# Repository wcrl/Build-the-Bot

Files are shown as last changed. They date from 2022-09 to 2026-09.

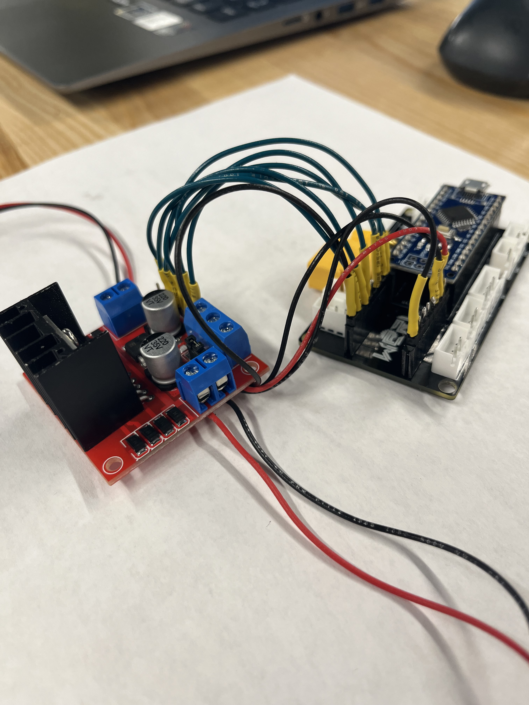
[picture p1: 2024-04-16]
WCRL Parts Library/Motor Drivers/L298N/Arduino Example/L298N_Side.jpg

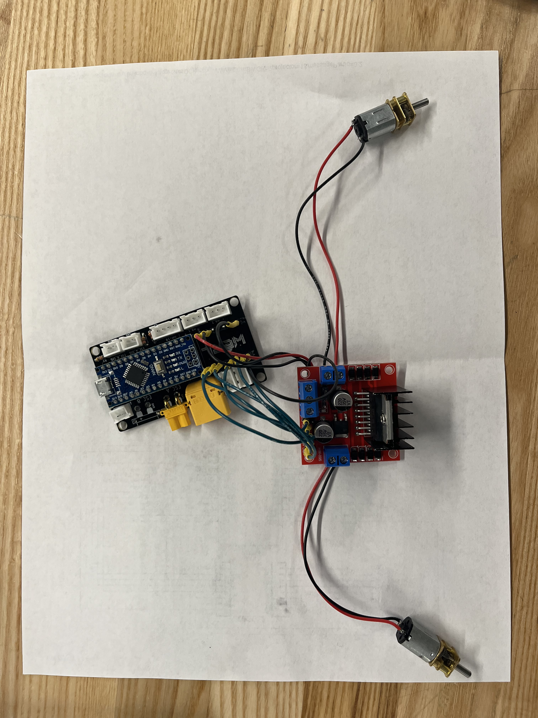
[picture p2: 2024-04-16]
WCRL Parts Library/Motor Drivers/L298N/Arduino Example/L298N_top.jpg

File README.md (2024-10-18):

# About WCRL
Our mission at the Watson Combat Robotics League is to empower collegiate students to develop technical engineering skills through competitive combat robotics. We aim to foster a community of innovation and creativity for students and enthusiasts by providing a platform for designing, building, and testing 3D printed robots in a safe and exciting environment. Our focus is on promoting STEM education by providing an opportunity for practical experience in mechanical design, electrical engineering, and programming as well as peer guidance and resources to make participation increasingly accessible. Through our league, we strive to cultivate the next generation of skilled engineers and innovators who will shape the future of technology and robotics.

# Build-the-Bot
Welcome to the Build-the-Bot platform! Build-the-Bot is an open-source Arduino based robotics platform maintained by the Watson Combat Robotics League at Binghamton University!

To get started, read the [Getting Started Guide](https://github.com/wcrl/Build-the-Bot/blob/453a59d6409c2aacc2f1eb8cd54fe76791a7de1f/Getting%20Started/Getting%20Started.md) and the [3D Printing Guide](https://github.com/wcrl/Build-the-Bot/blob/453a59d6409c2aacc2f1eb8cd54fe76791a7de1f/Getting%20Started/3D%20Printing%20Guide.md). From there, start designing and planning out your bot! 

### Check out our [Website](https://wcrl.github.io/)

### Join our [WCRL Discord](https://discord.gg/YJxM6xMASq)

In order to move to registered status and gain access to more channels make sure you
- Change your discord nickname in this server to your first and last name 
- Fill out our registration form via google forms: https://forms.gle/xkhhvzqmUq5xLZNm7

If you have any questions, please contact us via our discord, or email WCRL@binghamton.edu.

Happy Building!

# Future Development Plans 
- PCB for Battery Cutoff

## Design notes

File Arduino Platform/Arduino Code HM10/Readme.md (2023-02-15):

# ReadME

There are two different sets of code for Bot Control on the Arduino Platform. Due to lack of updates by Dabble, iPhones on iOS 16+ will need to utilize the BitBlue code.

## BitBlue

Note: Pressing and holding does NOT function properly. This is a design conflict in the
BitBlue application. Instead, pressing the button once will trigger an action. Pressing
the button again will end that action.

Controls:

- Forward Arrow: Move Bot Forward
- Back Arrow: Move Bot in Reverse
- Left Arrow: Move Bot to the Left
- Right Arrow: Move Bot to the Right
- A: Competition Attachment at Low Speed
- X: Competition Attachment at High Speed
- B: Not Used
- Y: Not Used
- Start: Not Used
- Select: Not Used

## Dabble

Controls:

- Forward Arrow: Move Bot Forward
- Back Arrow: Move Bot in Reverse
- Left Arrow: Move Bot to the Left
- Right Arrow: Move Bot to the Right
- Triangle: Competition Attachment at Low Speed
- Circle: Competition Attachment at High Speed
- X: Turn off Competition Attachment
- Square: Not Used
- Start: Not Used
- Select: Not Used

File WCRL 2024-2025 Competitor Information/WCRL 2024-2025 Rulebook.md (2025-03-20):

# Watson Combat Robotics League Fall 2024 - Spring 2025 Rulebook

## Version 4.2 | Revised 2025-02-07

## Overview

### Disclaimer

These rules are subject to change with revisions indicated by <u>underlined text</u> and a higher revision number posted above. Competitors will receive notice of changes through the official [WCRL Discord](https://discord.gg/YJxM6xMASq).

Questions answered by an Executive Board Member in the official WCRL discord serve as a revision to the rules and shall be treated as such until the next official revision of the rules is released. The WCRL Executive Board will not answer any rule-pertinent questions in private forms of communication, and if, for whatever reason, these questions are answered privately, they do not serve as official rulings and shall not be treated as such.

The Watson Combat Robotics League Judging Committee and Executive Board reserve the right to remove any team from matches, tournaments, or the league at any time for any reason (including, without limitation, failure to meet safety and/or technical requirements) in its sole and absolute discretion. It is the responsibility of each team to understand and abide by all rules herein.

### Scope

This document outlines the requirements for any team that intends to compete in the 2024-2025 Watson Combat Robotics League (WCRL) (Spring Specific), including the league’s competitions and tournaments.

The Watson Combat Robotics League is an officially recognized Thomas J. Watson College of Engineering and Applied Sciences Student Organization under the oversight of the Electrical and Computer Engineering Department and facilitated by the Watson Combat Robotics League Executive Board.

The following rules have been constructed to be as unrestrictive to the design process as possible while balancing fairness to other competitors, arena damage, scheduling issues, and the safety of any and all competitors, crew, and audience members. **Any discrepancies in the rules will be enforced based on the interpretation of the rules, as written, by the WCRL Executive Board.**

### Definitions

- **Arena:** The arena is approximately 1.83m x 1.83m x 0.91m (6ft x 6ft x 3ft). The arena is outlined in detail in section 6.
- **Bot:** Any movable combat robot that is designed by a WCRL team following the rules as they are outlined herein.
- **Competition:** Any event hosted by the WCRL in which two or more teams compete against each other**
- **Competition Attachment:** A movable, 3D printed component that is attached to a bot that can seriously hinder, halt, or otherwise disrupt the operation of another bot (I.E., a bot's weapon).
- **Control System:** Any device used to send user input to the Bot, i.e. a remote control.
- **Executive Board:** The governing body of the Watson Combat Robotics League, listed in section 4.1.
- **Inspection Checklist:** A document provided to teams prior to the tournament and/or any subsequent tournaments that outlines the most common rule violations to help ensure bots are in compliance with the rules contained herein.
- **Inspection Period:** A portion of the tournament, and/or any subsequent tournaments, in which bots are weighed, measured, and are otherwise verified to abide by these rules. Any bots who do not pass inspection by the end of the inspection period are **not** eligible to demonstrate/compete on that day.  
  - **Note: WCRL Executive Board Officers will be holding open lab hours weekly leading up to the competition and can inspect bots to ensure rule compliance upon team request.**
- **Judging Panel:** The judges of the tournament. These judges will determine the winner of individual matches, and decide two of the three awards, as indicated in section 3.3.
- **League:** The league refers to the entire 2024-2025 competition season
- **Power Switch:** Mechanically and directly shuts off power to the entire bot as explained in section 5.8.
- **Tournament:** A larger competition hosted by the WCRL one weekend per semester.**
- **BOM:** Bill of materials, a complete list of all component parts on the bot including specifications, number of items, and prices.

### Executive Board

- Chairperson: [John Pforte](jpforte1@binghamton.edu)
- League Coordinator: [Ryan Calhoun](rcalhou1@binghamton.edu) 
- Build Technicians: [Sam Abramson](sabrams5@binghamton.edu) | [Ben Sharples](bsharpl1@binghamton.edu) | [Walter Schutz](wschutz1@binghamton.edu) | [Melanie Koren](mkoren1@binghamton.edu) | [Erick Palka](epalka@binghamton.edu) | [Salaj Rijal](srijal@binghamton.edu) | [Mckenzie Viersma](mviersm1@binghamton.edu)
- Competition Coordinator: [Rohan Bajwa](rbajwa1@binghamton.edu)
- Outreach Coordinator: [Haiden Danto-Scanlan](hdantos1@binghamton.edu)
- Social Media Coordinator: [Xinlin Wu](xwu19@binghamton.edu)
- First-Year Ambassadors: [Jay Akasofu](jakasofu@binghamton.edu) | [Alexander Sosa](asosa@binghamton.edu) | [Xinlin Wu](xwu19@binghamton.edu)
- Faculty Advisor: [Professor Wenfeng Zhao](wzhao@binghamton.edu)

### Judging Committee 

- [Professor Douglas Summerville](dsummer@binghamton.edu) (ECE)
- [Professor Scott Craver](Scraver@Binghamton.edu) (ECE)
- [Professor Wenfeng Zhao](wzhao@binghamton.edu) (ECE | Faculty Advisor)
- [Professor Koenraad Gieskes](gieskes@binghamton.edu) (EDD)
- [Professor Melissa Simonik](msimonik@binghamton.edu) (EDD)

_Due to potential scheduling conflicts, the judging committee is subject to change at any time without formal notice in this rulebook. In the event of a tie, a member of the Executive Board will act as the tie-breaking vote._

### Competitors

Teams must register to compete in the WCRL by having each member of their team complete the Google Form Registration and join the Discord. Once all members are registered, the team can reach out to the Eboard with their members and team name, to officially register a team.

Official bot name, team name, and attachment file names must be school-appropriate and cannot contain the word “weapon” or reference to weapons.

- Team and bot names are subject to Executive Board approval.
- Teams may compete with multiple bots if the following criteria are met:
  - Each bot satisfies the requirements.
  - The sum of all robot weights are less than the 1 lb weight limit.

---

## League Overview

The league refers to the entire 2024-2025 competition seasons. During this time teams will brainstorm designs, prototype their design, build bots, compete, and rebuild bots.

### Matches

There will six qualifying competitions per season, held in the Thomas J. Watson College of Engineering and Applied Sciences Fabrication Lab - Engineering Building E1. Two or more teams will compete against each other at each competition, with the competition being live-streamed.

Dates for qualifying competitions and tournaments can be found on our public [WCRL Event Calendar](https://calendar.google.com/calendar/u/0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).

Matches are 2 minutes long, but may be called early for safety concerns or if a winner is decided based on the below criteria.

Pinning:

- For the first 1 minute: A bot can pin another bot for a maximum of 5 seconds before having to release the bot for a minimum of 5 seconds. The 8 second limit will be counted down by the WCRL Executive Board member in charge of the match.
- With less than 60 seconds remaining: If a bot is pinned for more than 5 seconds, the pinned bot will lose. The 5 second limit will be counted down by the WCRL Executive Board member in charge of the match.
  - For teams competing with multiple bots, the rules on pinning are as follows:
    - If bots are equal weights: All bots must be pinned. If a bot is pinned during the eligible time, it may no longer be used.
    - If bots are unequal weights: A majority of the weight must be pinned in order to win. 

Bot Control:

- Bots who lose mobility will lose the match following the same 5 second countdown (i.e., you are not pinned, but your wheels stop being able to move your bot).
- Bots are allowed to lose the ability to control their competition attachment after the initial inspection (outlined below) without forfeiting the match.

### Tournament

There will be one tournament per semester, held in the Binghamton University Innovative Technologies Complex Rotunda. The tournament will run from approximately 9:00 am to 3:00 pm. To be eligible to compete in the tournament, teams must either win one qualifying competition or compete in two qualifying competitions.

More information on the tournament will be released as it becomes available. Any teams not signed in by the end of the inspection period on the day of the tournament will **not** be allowed to compete.

### Awards

There will be three awards presented at the Tournaments, effectively serving as a 1st, 2nd, and 3rd place, respectively:

  1. **Competition Champion:** Presented to the team that wins the double-elimination bracket.
  2. **Competition Runner-Up:** Presented to the team that loses in the finals of the double elimination bracket.
  3. **WCRL Choice:** Presented to the team who excels in bot design, as selected by the judging panel and executive board based on a set of predetermined criteria.

---

## Bot Requirements

### Mobility

- All robots must have easily visible and controlled mobility in order to compete.
Methods of mobility include but are not limited to:
  - Rolling (wheels, tracks or the whole robot)
- No flying, hovering, or otherwise floating bots will be permitted.
  - If a bot is lifted from the floor in the normal course of the match, the bot will not be penalized.
  - Jumping bots are permitted.

### Core Specifications

- The maximum weight for any bot is 453 g (1 lb).
- The maximum height for any bot is determined by the height of the arena.
  - Suggested maximum height is 25 cm.
  - Bots can be weighed on scales made available by the WCRL Executive Board
  - There are no other size restrictions on bots.
    - Note: The arena is 1.83m x 1.83m x 0.91m (6ft x 6ft x 3ft), so keep this in mind for bot design (More on this in section 6.1).
- Each bot shall be entirely 3D printed with an approved 3D Printing material, outlined below:
  - Permissible 3D printing materials include: ABS, PLA (and PLA variants), PETG, Resin, and TPU. Filaments not listed must be approved by the Executive Board.
- The following items are exceptions to the 3D printed requirement: motors, wheels, electronics, axles, bearings, pins, fasteners, rubber bands, belts, adhesives
  - These items must be used in their intended fashion and can not be used to armor the bot
- Flex seal, duct tape, or similar products, are not allowed on the bot.
  - Paint may be allowed on the bot for the purpose of decoration only. Any paint or other coating that adds structural integrity is prohibited.
- Bots cannot intentionally damage the arena

### Competition Attachments (Weapons)

- All bots must have at least one independently powered, 3D printed competition attachment that can seriously affect the operation of another bot. (Note: Bots that have an attachment that cannot cause significant damage to another bot will be seen as _not_ having a competition attachment. This includes flippers that move, but cannot move the weight of the bot with enough power to cause damage).
  - A wedge is permissible, as long as it is accompanied by an additional active competition attachment.
  - Spinning weapons must come to a full stop within 60 seconds of the power
being removed using a self-contained braking system
  - Competition attachments may be swapped between matches, but may require re-inspection.
  - There is no limit on the number of competition attachments on a particular bot.
  - **The following items are not permitted under any circumstances:**
    - Competition attachments that are in any part enhanced with a non-3D printed material
    - Heat and fire are forbidden as weapons. This includes, but is not limited to the
following:
      - Flammable liquids or gases
      - Explosives or flammable solids such as:
        - DOT Class C Devices
        - Gunpowder
        - Cartridge Primers
        - Military explosives, etc.
    - Weapons that require significant cleanup, or in some way damages the arena to
require repair for further matches. This includes but is not limited to:
      - Foams and liquified gases
      - Powders, sand, ball bearings and other dry chaff weapons
    - Projectiles of any type.
    - Entangling Weapons or defenses: these are weapons or defenses that can
reasonably be expected to stop drive train and/or weapon motion by being
wrapped around rotating parts. This includes nets, tapes, strings, and other
entangling materials or devices.
    - Weapons designed to cause invisible damage to the other robot. This includes but is not limited to:
      - Electrical weapons
      - RF jamming equipment
      - RF noise generated by an IC engine
      - EMF fields from permanent/electro-magnets that affect another robot's electronics
    -  Light and smoke based weapons that impair the viewing of robots by an Entrant, Judge, Official or Viewer. This includes, but is not limited to:
       -  Smoke weapons
       -  Lasers
       -  Bright strobe lights
    - Competition attachments that purposefully detach from the bot and are left on the field.
    - Hydraulics or pneumatics.

If a team is concerned about their bot abiding by these rules, WCRL Executive Board members will be holding office hours weekly for the duration of the league. Specific design questions or concerns can also be addressed to any member of the WCRL Executive Board in a private chat.

### Electronics

- [Only LiPo Batteries](https://www.amazon.com/dp/B07Y67CHJT/?coliid=I34AU5484KJY88&colid=1XSIUG9AQPBZB&psc=1&ref_=lv_ov_lig_dp_it) that do not exceed 14 V (4s) nominally are allowed
  - Refer to Appendix 1 for more information on Battery Safety
- The maximum voltage anywhere on the bot is not to exceed 24V.
- Batteries must be sufficiently protected.
  - I.E., If one could jam the blade of a long screwdriver through gaps in the 3D printed shell/frame of the bot and hit the battery, it is not sufficiently protected.
- During the competition, the WCRL executive team will swap drained batteries for fully charged ones to prevent the need for any team to charge their own batteries.
  - If you do not use a WCRL provided battery, they must be charged using a proper battery bag and charger
  - These batteries will be available in designated areas the day of the tournament, and located in EB E1 during the league.
  - Teams must return the provided battery prior to utilizing another one.
- Teams using WCRL provided batteries must have under-voltage protections in place to prevent damaging the batteries. An under-voltage alert buzzer circuit will be available to teams to use in their designs.
- Bots must have a visible LED that is on whenever the bot is on.
- Kill Switches
  - All robots must be able to be FULLY deactivated, which includes power to
drive and weaponry, in under 60 seconds by a manual disconnect.

### Remote Control

- No signal jamming, or deliberate signal interference is permitted.
  - If using Bluetooth controls, renaming the Bluetooth transceiver and adding a password is required to prevent signal interference.
  - Taking control of another team's bot is prohibited
- All control systems must be in compliance with Federal Communications Commission (FCC) regulations, including only accessing and utilizing permitted channels.
- WCRL, WCRL partners, or WCRL sponsors are not liable if teams do not comply with FCC regulations.
- The type and manner of power supply for the controller are left to the team’s discretion as long as the selected design does not aid the performance of the bot beyond allowing driver input to reach the bot.
- There is no restriction on the number of drivers for any one bot as long as all drivers on a team are collectively controlling one single bot.

### Inspection Period

  Each bot will be evaluated for rule compliance by the WCRL Executive Board or other official staff prior to being admitted to any competition or tournament. Failure to comply with the rules or pass inspection may result in disqualification from the match, competition, or tournament.

  **The WCRL Executive Board has the right to refuse any bot deemed particularly dangerous or damaging to people or property.**

  Once a bot passes inspection, the bot will then have a quick inspection prior to each match. This inspection will ensure that the bot is mobile and has a functional competition attachment (as outlined above). _Both_ are required for a bot to be eligible to compete in the match.

### Arena

- The arena is 1.83m x 1.83m x 0.91m (6ft x 6ft x 3ft)
- Note: The floor of the arena is subject to change, and may not be perfectly flat. Testing is recommended prior to the competition to ensure your bot can traverse the arena successfully.
- Once the bot is placed inside the arena, there shall be no further physical interaction with the bot by team members.
- The arena may have additional active and passive field elements to contend with.

---

## 3D Printing

### General Rules

- These parts must not appear to be traditional weapons.
- These competition attachments file names must also not be named in such a way that makes them sound like weapons. (I.e., do not name the item “Blade” or “Knife”).
- Print as soon as possible; there may be delays due to the printing of senior projects which take priority.
- The Watson Combat Robotics League does not print parts for teams nor pay for parts printed by teams.

### Watson Fabrication Lab (Binghamton University Specific)

- Teams can submit models to be printed in the Watson Fabrication Lab by completing the “Request for Fabrication” form posted in the Fabrication lab.
- By printing in the Fabrication Lab, teams agree to any and all Fabrication Lab rules and regulations.

### Emerging Technology Studio (ETS) (Binghamton University Specific)

- [Click here for more information on the ETS.](https://www.binghamton.edu/its/about/organization/technology-support-services/innovation/ets/index.html)
  - Capabilities of printers as well as the print process is outlined on the aforementioned website.
- By printing in the ETS, teams agree to any and all ETS rules and regulations.
- Teams are responsible for the cost of all 3D prints. ETS policy has prints charged to a student’s BUC$ account.
- It is advisable for teams to buy their own filament, and bring it to the ETS, as then there would be no charge to use ETS printers.

---

## Testing

- An arena will be available in the Watson Fabrication Lab (E1)
- A bot's competition attachment can only be tested if the bot is fully within the closed arena.
- This arena is available for use during standard Watson Fabrication Lab hours, or extended hours if a WCRL member is present
- The lid of the arena must be closed during the entirety of the test.
- Teams may use any empty shells in the arena for testing – these shells are in limited supply, and will not be replaced on any set schedule.
  - If your team has any failed bot shells, please consider donating them for other teams to test.
  - Scrimmages are allowed. Please let the WCRL executive team know if you are going to compete against another bot (we’d love to watch!)
  - If your bot starts smoking during one of the tests (not the battery smoking), unplug the battery as quickly and safely as possible.
  - If your battery catches fire, leave the bot where it is inside of the arena, clear the immediate area, and notify one of the shop technicians for assistance.
- If you are concerned about running a test, please run the test during WCRL office hours as we would be happy to assist you.

---

## Use of Workspace

- While using communal spaces such as the Watson Fabrication Lab, ITC, and other spaces, teams must be responsible for:
  - Ensuring all equipment is clean and put away in the proper place.
  - Ensuring that the workspace is properly cleaned.
- Damage to equipment or the arena during bot assembly or testing should be reported to the Executive Board or a shop technician.
- Not adhering to workspace maintenence guidelines will result in action from the Executive Board.  

## Finances

- Each team is limited to a budget cap of $125.
  - 3D printed parts will not be counted towards the budget due to the necessity of spares for multiple matches.
  - The $125 refers to parts on the bot at any given time. Spare parts are not included in the budget cap.
  - This maximum budget for bots includes all control systems, unless you are using a mobile device (cell phone, tablet) for controlling your bot or you have built the controller yourself. In which case, the device itself does not count in the budget.
- Donated or salvaged items must be recorded in the budget as costing an equivalent price to the same part online, sold and shipped by Amazon or Alibaba.
  - If there is any confusion on pricing, the final ruling will be made by the Executive Board.
- WCRL Partners (I.E., Watson student groups) can sponsor their respective teams with any amount of funding. However, each team is still subject to the budget cap.
- Teams must have receipts and a Bill of Materials of all of their parts and pricing available to be reviewed by a judge upon request. Failure to comply with these rules may result in disqualification of a team for award consideration.
  - Teams must use the provided BOM template with accurate pricing to be submitted 24 hours prior to the start of matches and/or tournaments.

---

## Resources

- Check out our [Getting Started Guide](https://github.com/wcrl/Build-the-Bot/blob/main/Getting%20Started/Getting%20Started.md)
- Check out our [Electronics Bill of Materials](https://github.com/wcrl/Build-the-Bot/blob/main/Electronics/Electronics%20BOM.md)

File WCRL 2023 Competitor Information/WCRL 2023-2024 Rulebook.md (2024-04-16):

# Watson Combat Robotics League Fall 2023 - Spring 2024 Rulebook

## Version 4.1 | Revised 2023-04-16

## Overview

### Disclaimer

These rules are subject to change with revisions indicated by <u>underlined text</u> and a higher revision number posted above. Competitors will receive notice of changes through the official [WCRL Discord](https://discord.gg/YJxM6xMASq).

Questions answered by an Executive Board Member in the official WCRL discord serve as a revision to the rules and shall be treated as such until the next official revision of the rules is released. The WCRL Executive Board will not answer any rule-pertinent questions in private forms of communication, and if, for whatever reason, these questions are answered privately, they do not serve as official rulings and shall not be treated as such.

The Watson Combat Robotics League Judging Committee and Executive Board reserve the right to remove any team from matches, tournaments, or the league at any time for any reason (including, without limitation, failure to meet safety and/or technical requirements) in its sole and absolute discretion. It is the responsibility of each team to understand and abide by all rules herein.

### Scope

This document outlines the requirements for any team that intends to compete in the 2023-2024 Watson Combat Robotics League (WCRL) (Spring Specific), including the league’s competitions and tournament.

The Watson Combat Robotics League is an officially recognized Thomas J. Watson College of Engineering and Applied Sciences Student Organization under the oversight of the Electrical and Computer Engineering Department and facilitated by the Watson Combat Robotics League Executive Board.

The following rules have been constructed to be as unrestrictive to the design process as possible while balancing fairness to other competitors, arena damage, scheduling issues, and the safety of any and all competitors, crew, and audience members. **Any discrepancies in the rules will be enforced based on the interpretation of the rules, as written, by the WCRL Executive Board.**

### Definitions

- **Arena:** The arena is approximately 1.83m x 1.83m x 0.91m (6ft x 6ft x 3ft). The arena is outlined in detail in section 6.
- **Bot:** Any movable combat robot that is designed by a WCRL team following the rules as they are outlined herein.
- **Competition:** Any event hosted by the WCRL in which two or more teams compete against each other**
- **Competition Attachment:** A movable, 3D printed component that is attached to a bot that can seriously hinder, halt, or otherwise disrupt the operation of another bot (I.E., a bot's weapon).
- **Control System:** Any device used to send user input to the Bot, i.e. a remote control.
- **Executive Board:** The governing body of the Watson Combat Robotics League, listed in section 4.1.
- **Inspection Checklist:** A document provided to teams prior to the tournament and/or any subsequent tournaments that outlines the most common rule violations to help ensure bots are in compliance with the rules contained herein.
- **Inspection Period:** A portion of the tournament, and/or any subsequent tournaments, in which bots are weighed, measured, and are otherwise verified to abide by these rules. Any bots who do not pass inspection by the end of the inspection period are **not** eligible to demonstrate/compete on that day.  
  - **Note: WCRL Executive Board Officers will be holding open lab hours weekly leading up to the competition and can inspect bots to ensure rule compliance upon team request.**
- **Judging Panel:** The judges of the tournament. These judges will determine the winner of individual matches, and decide two of the three awards, as indicated in section 3.3.
- **League:** The league refers to the entire 2023-2024 competition season
- **Power Switch:** Mechanically and directly shuts off power to the entire bot as explained in section 5.8.
- **Tournament:** A larger competition hosted by the WCRL one weekend per semester.**
- **BOM:** Bill of materials, a complete list of all component parts on the bot including specifications, number of items, and prices.

### Executive Board

- Chairperson: [John Pforte](jpforte1@binghamton.edu)
- Vice-Chairperson: [Luke Riddoch](lriddoc1@binghamton.edu)
- League Coordinator: [Ryan Calhoun](rcalhou1@binghamton.edu) 
- Build Technicians: [Sam Abramson](sabrams5@binghamton.edu) | [Edward Nunez](enunez10@binghamton.edu) | [Ben Sharples](bsharpl1@binghamton.edu) | [Walter Schutz](wschutz1@binghamton.edu) 
- Competition Coordinator: [David Stein](dstein8@binghamton.edu)
- Outreach Coordinator: [Haiden Danto-Scanlan](hdantos1@binghamton.edu)
- Social Media Coordinator: [Mckenzie Viersma](mviersm1@binghamton.edu)
- First-Year Ambassadors: [Melanie Koren](mkoren1@binghamton.edu) | [Erick Palka](epalka@binghamton.edu) | [Salaj Rijal](srijal@binghamton.edu) | [Timothy Tran](ttran14@binghamton.edu)
- Faculty Advisor: [Professor Wenfeng Zhao](wzhao@binghamton.edu)

### Judging Committee 

- [Professor Douglas Summerville](dsummer@binghamton.edu) (ECE)
- [Professor Scott Craver](Scraver@Binghamton.edu) (ECE)
- [Professor Wenfeng Zhao](wzhao@binghamton.edu) (ECE | Faculty Advisor)
- [Professor Koenraad Gieskes](gieskes@binghamton.edu) (EDD)
- [Professor Melissa Simonik](msimonik@binghamton.edu) (EDD)

_Due to potential scheduling conflicts, the judging committee is subject to change at any time without formal notice in this rulebook. In the event of a tie, a member of the Executive Board will act as the tie-breaking vote._

### Competitors

Teams must register to compete in the WCRL by having each member of their team complete the Google Form Registration and join the Discord. Once all members are registered, the team can reach out to the Eboard with their members and team name, to officially register a team.

Official bot name, team name, and attachment file names must be school-appropriate and cannot contain the word “weapon” or reference to weapons.

- Team and bot names are subject to Executive Board approval.
- Teams may compete with multiple bots if the following criteria are met:
  - Each bot satisfies the requirements.
  - The sum of all robot weights are less than the 1kg weight limit.

---

## League Overview

The league refers to the entire 2023-2024 competition seasons. During this time teams will brainstorm designs, prototype their design, build bots, compete, and rebuild bots.

### Matches

There will five matches a month held in the Thomas J. Watson College of Engineering and Applied Sciences Fabrication Lab - Engineering Building E1. Two or more teams will compete against each other at each competition, with the competition being live-streamed.

Dates for matches and tournaments can be found on our public [WCRL Event Calendar](https://calendar.google.com/calendar/u/0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).

Matches are 2 minutes long, but may be called early for safety concerns or if a winner is decided based on the below criteria.

Pinning:

- For the first 1 minute: A bot can pin another bot for a maximum of 5 seconds before having to release the bot for a minimum of 5 seconds. The 8 second limit will be counted down by the WCRL Executive Board member in charge of the match.
- With less than 60 seconds remaining: If a bot is pinned for more than 5 seconds, the pinned bot will lose. The 5 second limit will be counted down by the WCRL Executive Board member in charge of the match.
  - For teams competing with multiple bots, the rules on pinning are as follows:
    - If bots are equal weights: All bots must be pinned. If a bot is pinned during the eligible time, it may no longer be used.
    - If bots are unequal weights: A majority of the weight must be pinned in order to win. 

Bot Control:

- Bots who lose mobility will lose the match following the same 5 second countdown (i.e., you are not pinned, but your wheels stop being able to move your bot).
- Bots are allowed to lose the ability to control their competition attachment after the initial inspection (outlined below) without forfeitting the match.

### Tournament

There will be one tournament per semester, held in the Binghamton University Innovative Technologies Complex Rotunda. The tournament will run from approximately 9:00 am to 3:00 pm. To be eligible to compete in the tournament, teams must either win one qualifying competition or compete in two qualifying competitions.

More information on the tournament will be released as it becomes available. Any teams not signed in by the end of the inspection period on the day of the tournament will **not** be allowed to compete.

### Awards

There will be three awards presented at the Tournaments, effectively serving as a 1st, 2nd, and 3rd place, respectively:

  1. **Competition Champion:** Presented to the team that wins the double-elimination bracket.
  2. **Competition Runner-Up:** Presented to the team that loses in the finals of the double elimination bracket.
  3. **WCRL Choice:** Presented to the team who excels in bot design, as selected by the judging panel and executive board based on a set of predetermined criteria.

---

## Bot Requirements

### Mobility

- The bot must move around in a controlled manner without causing intentional damage to the arena.
- No flying, hovering, or otherwise floating bots will be permitted.
  - If a bot is lifted from the floor in the normal course of the match, the bot will not be penalized.
  - Jumping bots are permitted.

### Bot Control

- The driver(s) must maintain control over all of the bot’s functions at any given time.
- There is **not** an autonomous portion of this competition. This is subject to change in future competitions.

### Core Specifications

- The maximum weight for any bot is 1,000g (1kg).
- The maximum height for any bot is determined by the height of the arena.
  - Suggested maximum height is 25 cm.
  - Bots can be weighed on scales made available by the WCRL Executive Board
  - There are no other size restrictions on bots.
    - Note: The arena is 1.83m x 1.83m x 0.91m (6ft x 6ft x 3ft), so keep this in mind for bot design (More on this in section 6.1).
- Each bot shall be entirely 3D printed with an approved 3D Printing material, outlined below:
  - Permissible 3D printing materials include: ABS, PLA (and PLA variants), PETG, Resin, and TPU. Filaments not listed must be approved by the Executive Board.
- The following items are exceptions to the 3D printed requirement: motors, wheels, electronics, axles, bearings, pins, fasteners, rubber bands, belts, adhesives
  - These items must be used in their intended fashion and can not be used to armor the bot
- Flex seal, duct tape, or similar products, are not allowed on the bot.
  - Paint may be allowed on the bot for the purpose of decoration only. Any paint or other coating that adds structural integrity is prohibited.
- Bots cannot intentionally damage the arena

### Competition Attachments (Weapons)

- All bots must have at least one independently powered, 3D printed competition attachment that can seriously affect the operation of another bot. (Note: Bots that have an attachment that cannot cause significant damage to another bot will be seen as _not_ having a competition attachment. This includes flippers that move, but cannot move the weight of the bot with enough power to cause damage).
  - A wedge is permissible, as long as it is accompanied by an additional active competition attachment.
  - Competition attachments may be swapped between matches, but may require re-inspection.
  - There is no limit on the number of competition attachments on a particular bot.
  - **The following items are not permitted under any circumstances:**
    - Competition attachments that are in any part enhanced with a non-3D printed material
    - Fire/heat.
    - Liquids.
    - Projectiles of any type.
    - Fouling devices such as, but not limited to, glue, nets, fishing line, ball bearings, particulates, etc.
    - EMP generators or other devices intended to damage or jam the opponent bot’s electronics.
    - Bright lights, lasers, deliberate smoke generators, etc., that are distracting or dangerous to vision.
    - Competition attachments that purposefully detach from the bot and are left on the field.
    - Hydraulics or pneumatics.

If a team is concerned about their bot abiding by these rules, WCRL Executive Board members will be holding office hours weekly for the duration of the league. Specific design questions or concerns can also be addressed to any member of the WCRL Executive Board in a private chat.

### Electronics

- [Only LiPo Batteries](https://www.amazon.com/dp/B07Y67CHJT/?coliid=I34AU5484KJY88&colid=1XSIUG9AQPBZB&psc=1&ref_=lv_ov_lig_dp_it) that do not exceed 14 V (4s) nominally are allowed
  - Refer to Appendix 1 for more information on Battery Safety
- The maximum voltage anywhere on the bot is not to exceed 24V.
- Batteries must be sufficiently protected.
  - I.E., If one could jam the blade of a long screwdriver through gaps in the 3D printed shell/frame of the bot and hit the battery, it is not sufficiently protected.
- During the competition, the WCRL executive team will swap drained batteries for fully charged ones to prevent the need for any team to charge their own batteries.
  - If you do not use a WCRL provided battery, they must be charged using a proper battery bag and charger
  - These batteries will be available in designated areas the day of the tournament, and located in EB E1 during the league.
  - Teams must return the provided battery prior to utilizing another one.
- Teams using WCRL provided batteries must have under-voltage protections in place to prevent damaging the batteries. An under-voltage alert buzzer circuit will be available to teams to use in their designs.
- Bots must have a visible LED that is on whenever the bot is on.
- Power Switches
  - There must be a Power Switch on the bot.
    - The power switch must be located on the exterior of the bot
      - Power Switch operation must be simple enough to allow anyone present to use it.
      - Normal Power switch operation cannot require any lifting or tilting of the bot.
      - Switch operation cannot require that a person get in the path of any competition attachment.
      - No tools must be required to utilize the Power Switch.
      - An insertable/removable jumper plug is an approved (and preferred) alternative to other types of Power Switch.

### Remote Control

- No signal jamming, or deliberate signal interference is permitted.
  - If using Bluetooth controls, renaming the Bluetooth transceiver and adding a password is required to prevent signal interference.
  - Taking control of another team's bot is prohibited
- All control systems must be in compliance with Federal Communications Commission (FCC) regulations, including only accessing and utilizing permitted channels.
- WCRL, WCRL partners, or WCRL sponsors are not liable if teams do not comply with FCC regulations.
- The type and manner of power supply for the controller are left to the team’s discretion as long as the selected design does not aid the performance of the bot beyond allowing driver input to reach the bot.
- There is no restriction on the number of drivers for any one bot as long as all drivers on a team are collectively controlling one single bot.

### Inspection Period

  Each bot will be evaluated for rule compliance by the WCRL Executive Board or other official staff prior to being admitted to any competition or tournament. Failure to comply with the rules or pass inspection may result in disqualification from the match, competition, or tournament.

  **The WCRL Executive Board has the right to refuse any bot deemed particularly dangerous or damaging to people or property.**

  Once a bot passes inspection, the bot will then have a quick inspection prior to each match. This inspection will ensure that the bot is mobile and has a functional competition attachment (as outlined above). _Both_ are required for a bot to be eligible to compete in the match.

### Arena

- The arena is 1.83m x 1.83m x 0.91m (6ft x 6ft x 3ft)
- Note: The floor of the arena is subject to change, and may not be perfectly flat. Testing is recommended prior to the competition to ensure your bot can traverse the arena successfully.
- Once the bot is placed inside the arena, there shall be no further physical interaction with the bot by team members.
- The arena may have additional active and passive field elements to contend with.

---

## 3D Printing

### General Rules

- These parts must not appear to be traditional weapons.
- These competition attachments file names must also not be named in such a way that makes them sound like weapons. (I.e., do not name the item “Blade” or “Knife”).
- Print as soon as possible; there may be delays due to the printing of senior projects which take priority.
- The Watson Combat Robotics League does not print parts for teams nor pay for parts printed by teams.

### Watson Fabrication Lab (Binghamton University Specific)

- Teams can submit models to be printed in the Watson Fabrication Lab by completing the “Request for Fabrication” form posted in the Fabrication lab.
- By printing in the Fabrication Lab, teams agree to any and all Fabrication Lab rules and regulations.

### Emerging Technology Studio (ETS) (Binghamton University Specific)

- [Click here for more information on the ETS.](https://www.binghamton.edu/its/about/organization/technology-support-services/innovation/ets/index.html)
  - Capabilities of printers as well as the print process is outlined on the aforementioned website.
- By printing in the ETS, teams agree to any and all ETS rules and regulations.
- Teams are responsible for the cost of all 3D prints. ETS policy has prints charged to a student’s BUC$ account.
- It is advisable for teams to buy their own filament, and bring it to the ETS, as then there would be no charge to use ETS printers.

---

## Testing

- An arena will be available in the Watson Fabrication Lab (E1)
- A bot's competition attachment can only be tested if the bot is fully within the closed arena.
- This arena is available for use during standard Watson Fabrication Lab hours, or extended hours if a WCRL member is present
- The lid of the arena must be closed during the entirety of the test.
- Teams may use any empty shells in the arena for testing – these shells are in limited supply, and will not be replaced on any set schedule.
  - If your team has any failed bot shells, please consider donating them for other teams to test.
  - Scrimmages are allowed. Please let the WCRL executive team know if you are going to compete against another bot (we’d love to watch!)
  - If your bot starts smoking during one of the tests (not the battery smoking), unplug the battery as quickly and safely as possible.
  - If your battery catches fire, leave the bot where it is inside of the arena, clear the immediate area, and notify one of the shop technicians for assistance.
- If you are concerned about running a test, please run the test during WCRL office hours as we would be happy to assist you.

---

## Use of Workspace

- While using communal spaces such as the Watson Fabrication Lab, ITC, and other spaces, teams must be responsible for:
  - Ensuring all equipment is clean and put away in the proper place.
  - Ensuring that the workspace is properly cleaned.
- Damage to equipment or the arena during bot assembly or testing should be reported to the Executive Board or a shop technician.
- Not adhering to workspace maintenence guidelines will result in action from the Executive Board.  

## Finances

- Each team is limited to a budget cap of $125.
  - 3D printed parts will not be counted towards the budget due to the necessity of spares for multiple matches.
  - The $125 refers to parts on the bot at any given time. Spare parts are not included in the budget cap.
  - This maximum budget for bots includes all control systems, unless you are using a mobile device (cell phone, tablet) for controlling your bot or you have built the controller yourself. In which case, the device itself does not count in the budget.
- Donated or salvaged items must be recorded in the budget as costing an equivalent price to the same part online, sold and shipped by Amazon or Alibaba.
  - If there is any confusion on pricing, the final ruling will be made by the Executive Board.
- WCRL Partners (I.E., Watson student groups) can sponsor their respective teams with any amount of funding. However, each team is still subject to the budget cap.
- Teams must have receipts and a Bill of Materials of all of their parts and pricing available to be reviewed by a judge upon request. Failure to comply with these rules may result in disqualification of a team for award consideration.
  - Teams must use the provided BOM template with accurate pricing to be submitted 24 hours prior to the start of matches and/or tournaments.

---

## Resources

- Check out our [Getting Started Guide](https://github.com/wcrl/Build-the-Bot/blob/main/Getting%20Started/Getting%20Started.md)
- Check out our [Electronics Bill of Materials](https://github.com/wcrl/Build-the-Bot/blob/main/Electronics/Electronics%20BOM.md)

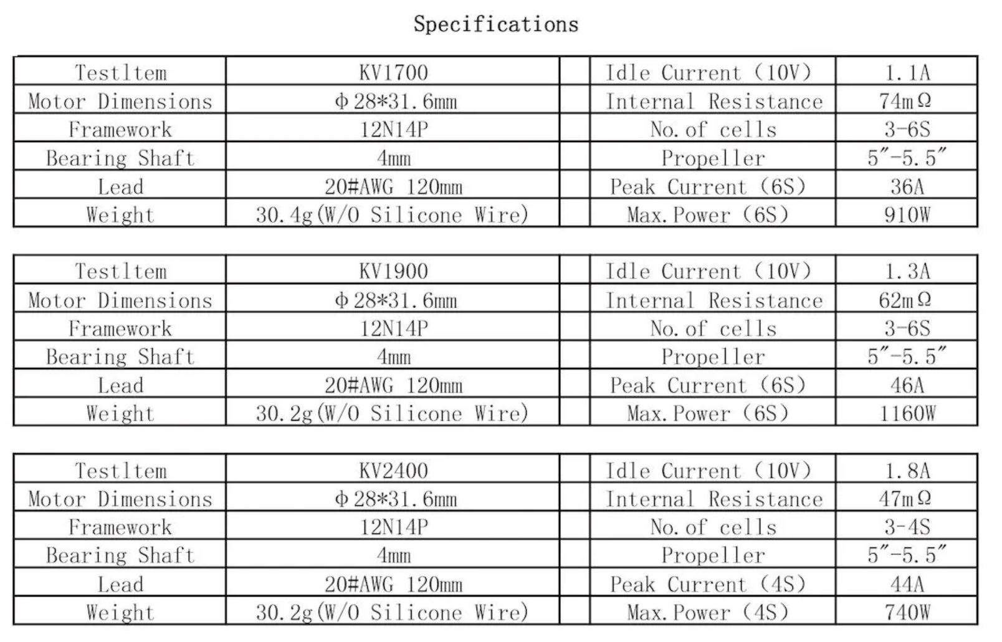
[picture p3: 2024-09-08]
WCRL Parts Library/BLDC Motors/EMAX ECO II Series 2306/EMAX ECO II Series 2306 Specs.png

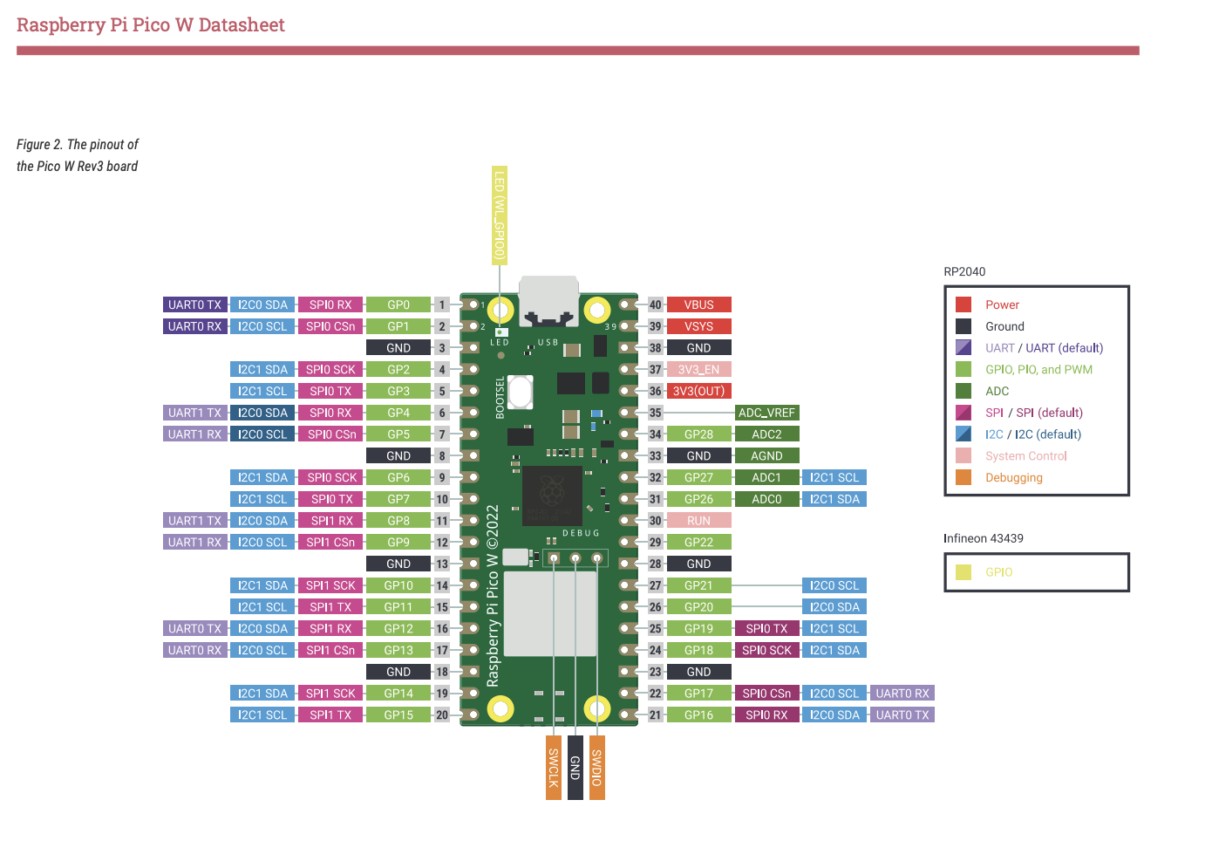
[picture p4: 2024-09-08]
WCRL Parts Library/Microcontrollers/Raspberry Pi Pico W/Pico W Pinout.png

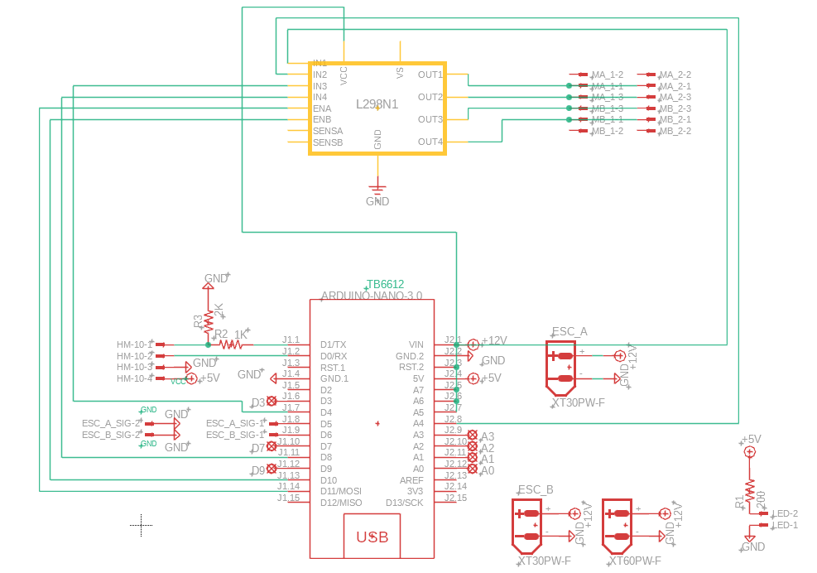
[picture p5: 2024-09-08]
WCRL Parts Library/Motor Drivers/L298N/Arduino Example/L298_Schematic.png

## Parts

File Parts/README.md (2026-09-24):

# Parts

Here are some CAD files for the parts that we provide. Note, not all the parts we provide are uploaded here yet.

For an up-to-date list of the parts we provide please check: https://docs.google.com/spreadsheets/u/1/d/e/2PACX-1vSNWbIkeQH0NxQ_KGRiqFoHKELZ4s0TO38RuMXRRxh4_Vu6C9dmzgX4YWMKjfzwMRgNfJxg5LBQq7SH/pubhtml

### Currently Uploaded
- EMAX ECO II Series 2306 Motor
    - BLDC motor intended to be used for spinner-based weapons
- N20 Motors
    - Brusehd motor intended to be used for drive systems

### Not Uploaded
- MG996R Motor (15kg/cm)
    - Servo motor intended to be used for flipper-based weapons
- OVONIC 3S Battery 650mah
    - LiPO battery used to power the robot

- WCRL Custom PCB
    - The custom WCRL pcb designed for our league's combat robots

- Ball Bearings
- Bearings
- Shafts
- Belts
- Pulleys

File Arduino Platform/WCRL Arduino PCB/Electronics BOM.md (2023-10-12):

# Electronics Bill of Materials
This is a recommended Bill-Of-Materials for the electronics of your bot. Parts in the category "PCB" are required to populate the PCB. All other parts are up to your preference.

*If you are a Thomas J. Watson College of Engineering and Applied Sciences student competing in the 2022-2023 Watson Combat Robotics League, these parts are provided for you on the WCRL shelf in EB B1. Please contact @executive in the discord with any questions.

| Category | Part Name | Part Description | Quantity | Unit Cost | Total Cost | Primary Link |
| --- | --- | --- | --- | --- | --- | --- |
| PCB | PCB* | WCRL\_Board\_V3 | 1 | $1.00 | $1.00 | [Github Link](https://github.com/wcrl/Build-the-Bot/tree/main/Electronics/Build-the-Bot%20PCB) |
| PCB | TB6612FNG DC Motor driver* | DC Motor Driver | 1 | $14.06 | $14.06 | [Digikey Link](https://www.digikey.com/en/products/detail/sparkfun-electronics/ROB-14451/7915577) |
| PCB | Arduino Nano* | Mini Nano V3.0 Module ATmega328P 5V 16MHz CH340G Chip Microcontroller Development Board for Arduino Without USB Cable | 1 | Price varies $5-$25 | $8.33 (estimated) | [Amazon Link](https://www.amazon.com/ELEGOO-Arduino-ATmega328P-Without-Compatible/dp/B0713XK923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) |
| PCB | Female Header Pins* | Cut the length of the Female header pins to the length required for the Nano and TB6612FNG | 4 | $0.18 | $0.72 | [Amazon Link](https://www.amazon.com/Qunqi-2-54mm-Straight-Connector-Arduino/dp/B07CGGSDWF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) |
| PCB | 1k Resistor* | 1k Resistor | 1 | $0.02 | $0.10 | [Digikey Link](https://www.digikey.com/en/products/detail/yageo/CFR-12JB-52-1K/4000) |
| PCB | 2k Resistor* | 2k Resistor | 1 | $0.02 | $0.10 | [Digikey Link](https://www.digikey.com/en/products/detail/yageo/CFR-12JR-52-2K/17662) |
| PCB | 200 Ohm Resistor* | 200 Ohm Resistor | 1 | $0.02 | $0.10 | [Digikey Link](https://www.digikey.com/en/products/detail/yageo/CFR-12JB-52-200R/2015) |
| PCB | JST-XH 2 Pin* | JST-XH 2 Pin | 3 | $0.03 | $0.09 | [Amazon Link](https://www.amazon.com/gp/product/B0731NHS9R/ref=ppx_yo_dt_b_search_asin_title?ie=UTF8&psc=1) |
| PCB | JST-XH 3 Pin* | JST-XH 3 Pin | 4 | $0.03 | $0.12 | [Amazon Link](https://www.amazon.com/gp/product/B0731NHS9R/ref=ppx_yo_dt_b_search_asin_title?ie=UTF8&psc=1) |
| PCB | JST-XH 4 Pin* | JST-XH 4 Pin | 1 | $0.03 | $0.03 | [Amazon Link](https://www.amazon.com/gp/product/B0731NHS9R/ref=ppx_yo_dt_b_search_asin_title?ie=UTF8&psc=1) |
| PCB | XT-30-PW-F* | XT30 Board Mount Connectors - Female | 2 | $0.96 | $1.92 | [Amazon Link](https://www.amazon.com/dp/B099F2PXYN?psc=1&ref=ppx_yo2ov_dt_b_product_details) |
| PCB | XT-60-PW-F* | XT60 Board Mount Connectors - Female | 1 | $2.00 | $2.00 | [Amazon Link](https://www.amazon.com/dp/B07VRLQ2C5?psc=1&ref=ppx_yo2ov_dt_b_product_details) |
| PCB | LED* | LED Indicator of Board Power | 1 | $0.30 | $0.30 | [Amazon Link](https://www.amazon.com/DiCUNO-450pcs-Colors-Emitting-Assorted/dp/B073QMYKDM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) |
| Battery | 11.1V 120C 1300mAh 3S Battery with XT60 Plug* | 11.1V Lipo Battery | 1 | $13.05 | $13.05 | [Amazon Link](https://www.amazon.com/Zeee-Graphene-Quadcopter-Helicopter-Airplane/dp/B07Y67CHJT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) |
| Bluetooth Transciever  | DSD TECH HM-10 Bluetooth 4.0 BLE iBeacon UART Module with 4PIN Base Board for Arduino UNO R3 Mega 2560 Nano | Bluetooth RX module | 1 | $10.99 | $10.99 | [Amazon Link](https://www.amazon.com/DSD-TECH-Bluetooth-iBeacon-Arduino/dp/B06WGZB2N4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) |
| BLDC | DJDK Brushless Motor 2300KV | Brushless Motor | -- | $15.99 | -- | [Amazon Link](https://www.amazon.com/DJDK-Brushless-RS2205-2300KV-Quadcopter/dp/B08Z7L3FC1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) |
| ESC | FLYCOLOR 30A Brushless ESC 2-4S with 5V 1A BEC for RC F450 Airplane Durable Quadcopter Helicopter | ESC for the BLDC Motors | -- | $15.99 | -- | [Amazon Link](https://www.amazon.com/FLYCOLOR-Brushless-Airplane-Quadcopter-Helicopter/dp/B09MDYS235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) |
| DC Motor | Fielect DC 6V 200RPM Mini Metal Gearwheel Micro Speed Reduction Motor Mini Gear Box Motor GA12-N20 | DC Motor: Also look for any similar motor that is around 200 RPM, affordable, timely, and n20 | -- | $13.40 | -- | [Amazon Link](https://www.amazon.com/Fielect-GA12-N20-200RPM-Reducer-Gearbox/dp/B08BZC7Y21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) |
| DC Motor | FingerTech "Silver Spark" 16mm Gearmotor 33:1 | DC Motor: [This is an alternative to the other DC Motor, for the price increase they are slightly more durable] | -- | $18.69 | -- | [Palm Beach Bots](https://palmbeachbots.com/products/fingertech-silver-spark-16mm-gearmotor-33-1?_pos=1&_sid=1a44c4297&_ss=r) | 
| Servo Motor | Miuzei 20KG Servo Motor High Torque RC Servo Metal Gear Waterproof for R/C Model DIY Car Robot, DS3218, Control Angle 270° | Combat attachment motor for rotations of a precise angle at high torque [Optional Alternative to BLDC] | -- | $12.99 | -- | [Amazon Link](https://www.amazon.com/Miuzei-Torque-Digital-Waterproof-Control/dp/B07HNTKSZT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) |
| Power Switch | XT60H (XT60 Upgrade) Male Female Bullet Connectors* | 2 Pairs of connectors for the power switch | 2 | $0.67 | $1.34 | [Amazon Link](https://www.amazon.com/dp/B07VRZR5TL?psc=1&ref=ppx_yo2ov_dt_b_product_details) |
| Power Switch | BNTECHGO 12 Gauge Silicone wire spool red and black* | 1 ft red, 1 ft black | 1 | $1.20 | $1.20 | [Amazon Link](https://www.amazon.com/dp/B01CJJU6NU?psc=1&ref=ppx_yo2ov_dt_b_product_details) |
| Power Switch | XT60EW-M Mountable XT60E Male Plug* | Need male OR female | 1 | $1.00 | $1.00 | [Amazon Link](https://www.amazon.com/dp/B09128LHGG?psc=1&ref=ppx_yo2ov_dt_b_product_details) [Amazon Link](https://www.amazon.com/gp/product/B09SL2MNN1/ref=ppx_yo_dt_b_search_asin_title?ie=UTF8&psc=1) | 
| ESC to BLDC Connectors | MR30 Connectors* | Need 1 for each ESC to BLDC Connections |  -- | $1 | -- | [Amazon Link](https://www.amazon.com/gp/product/B0747MW9RX/ref=ppx_yo_dt_b_search_asin_title?ie=UTF8&psc=1) |

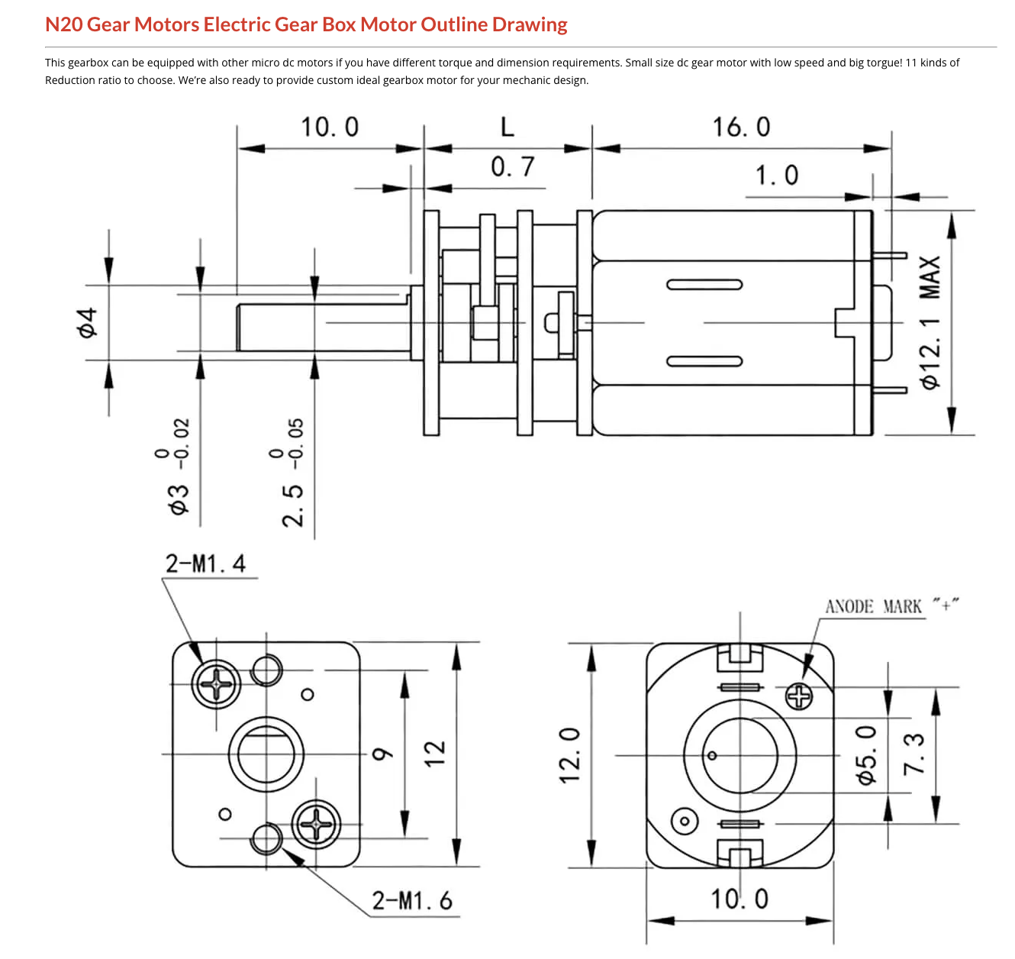
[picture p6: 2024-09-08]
WCRL Parts Library/DC Motors/N20/N20 Drawing.png

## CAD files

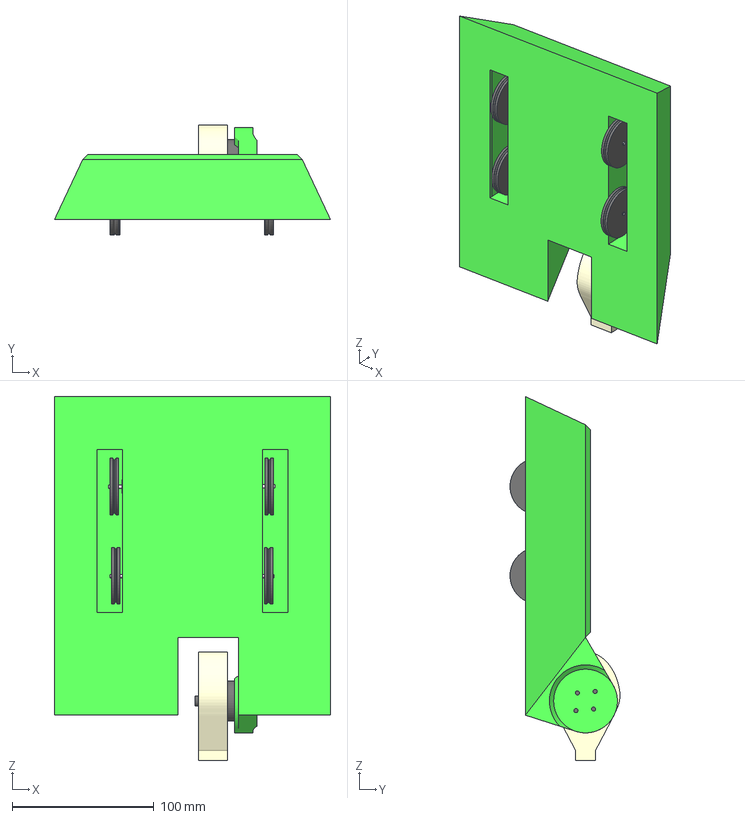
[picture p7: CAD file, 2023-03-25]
Getting Started/Sample CAD Files/Basic Bot Build/Basic Bot Build Assembly.3mf
195.0 x 77.6 x 257.0 mm
22x2 O-Ring x 4
BLDC
BasicBotBuildBody
Battery
DC Motor x 4
Lid
Motor Clamp x 4
Spinner
Wheel x 4

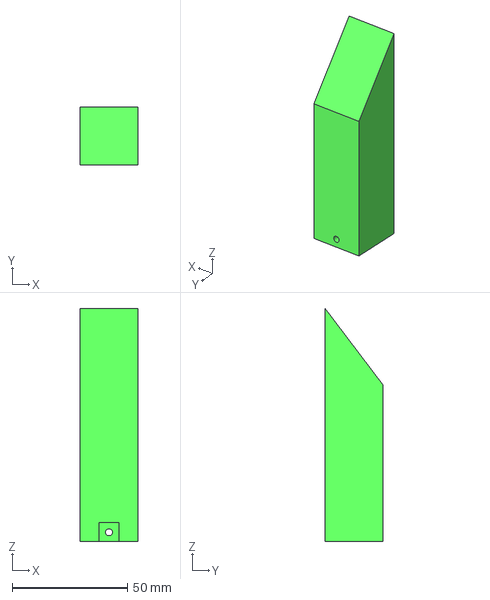
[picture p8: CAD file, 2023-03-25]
Getting Started/Sample CAD Files/Basic Bot Build/Plow.3mf
25.0 x 25.0 x 101.0 mm

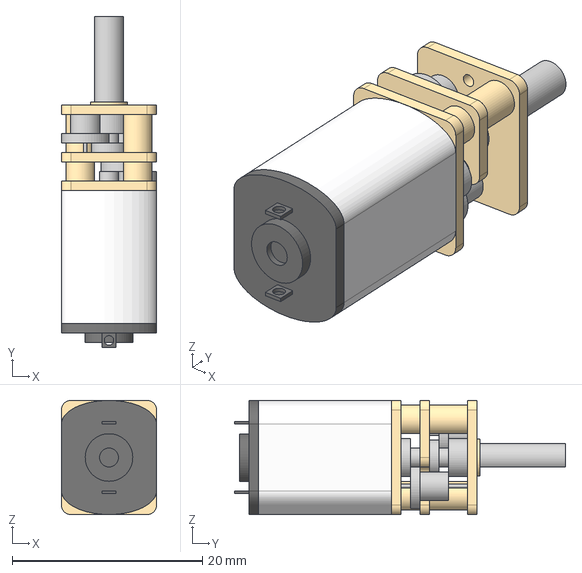
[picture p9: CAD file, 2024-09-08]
WCRL Parts Library/DC Motors/N20/N20 Motor.step
10.0 x 34.8 x 12.0 mm

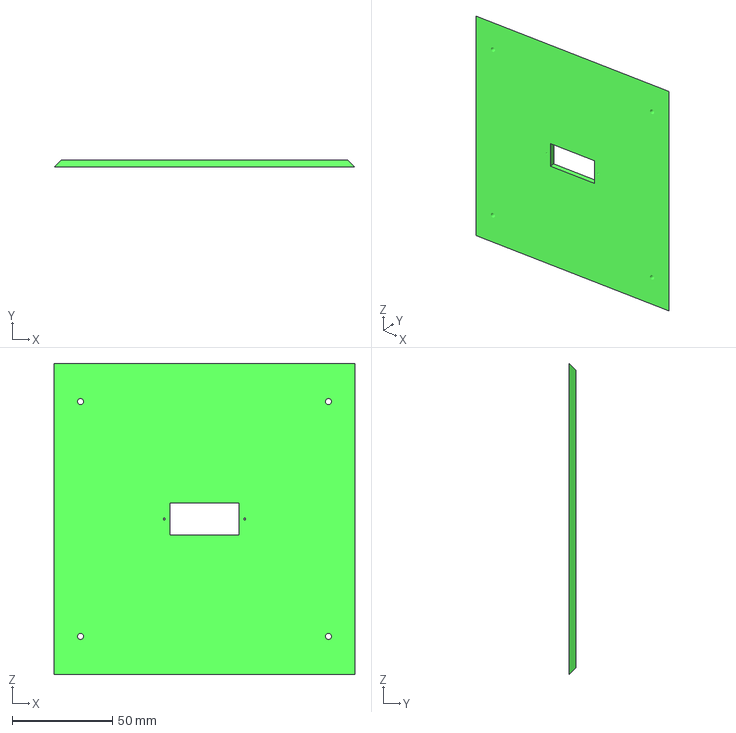
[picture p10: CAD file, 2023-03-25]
Getting Started/Sample CAD Files/Basic Bot Build/Basic Bot Build Lid.3mf
150.0 x 3.50 x 155.0 mm

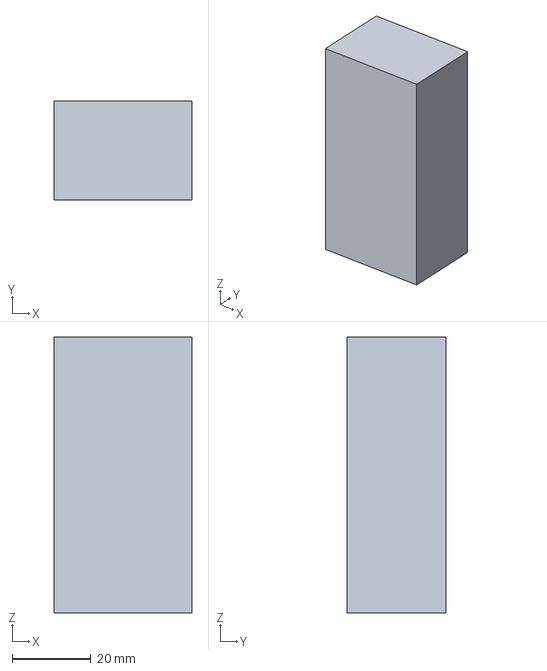
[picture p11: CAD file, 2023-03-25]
Getting Started/Sample CAD Files/Basic Bot Build/Battery.3mf
35.0 x 25.0 x 70.0 mm

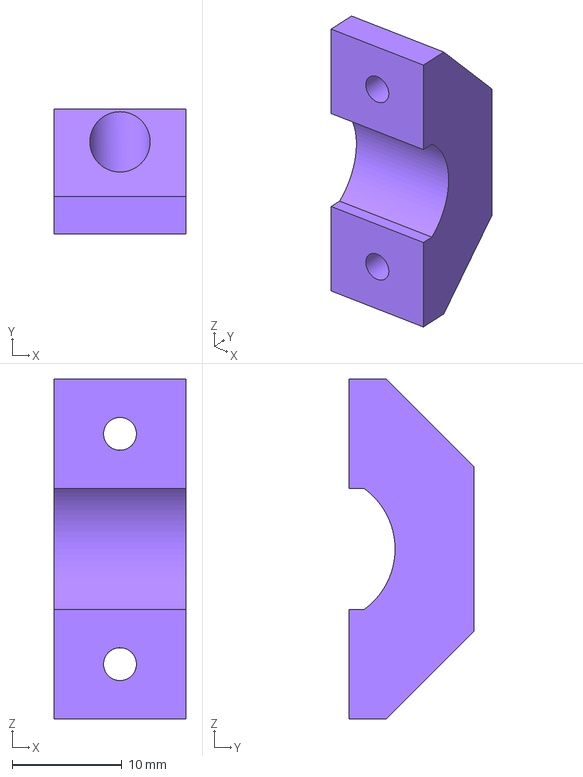
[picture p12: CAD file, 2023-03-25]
Getting Started/Sample CAD Files/Basic Bot Build/Motor Clamp.3mf
12.0 x 11.4 x 31.0 mm

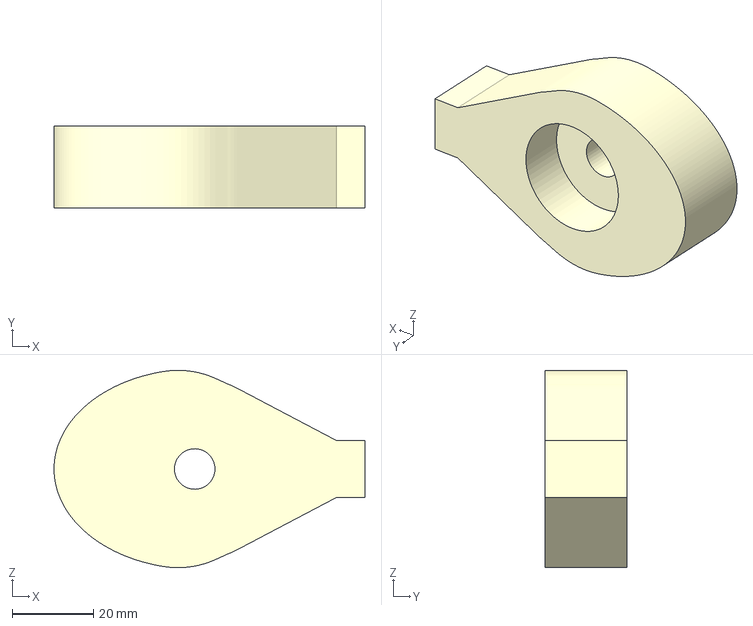
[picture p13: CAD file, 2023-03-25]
Getting Started/Sample CAD Files/Basic Bot Build/Spinner.3mf
76.7 x 20.2 x 48.6 mm

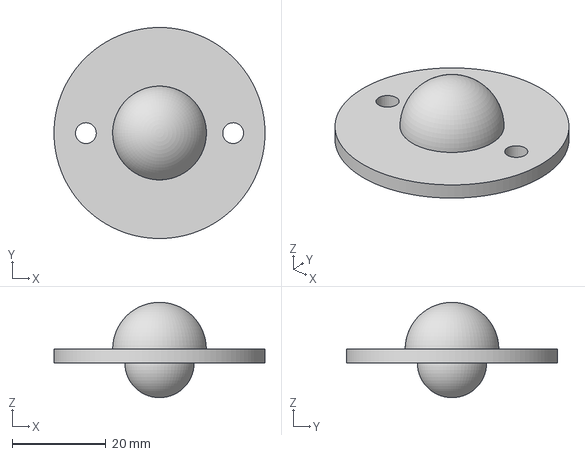
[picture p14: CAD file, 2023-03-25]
Getting Started/Sample CAD Files/Basic Bot Build/Ball Bearing.3mf
45.0 x 45.0 x 20.3 mm

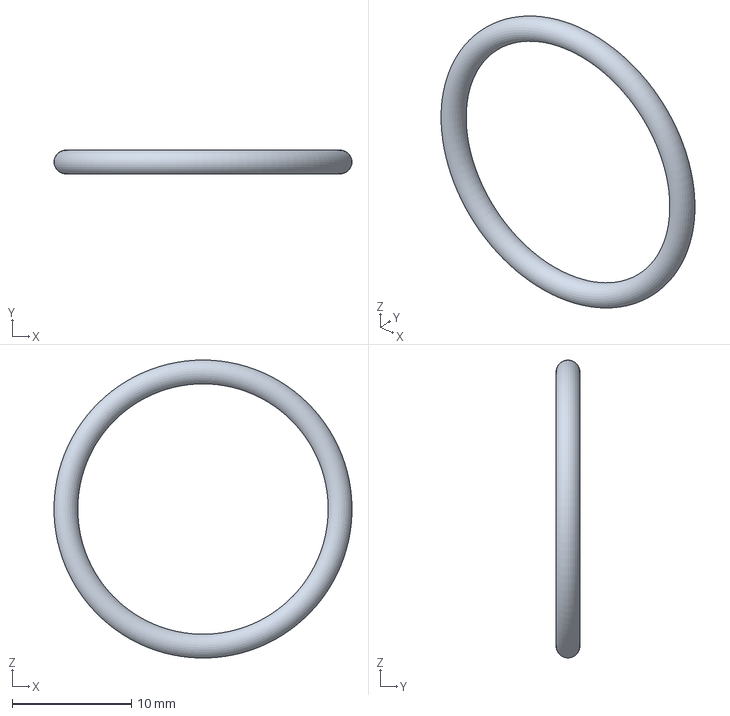
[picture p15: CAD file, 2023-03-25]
Getting Started/Sample CAD Files/Basic Bot Build/22x2 O Ring.3mf
25.0 x 1.99 x 25.0 mm

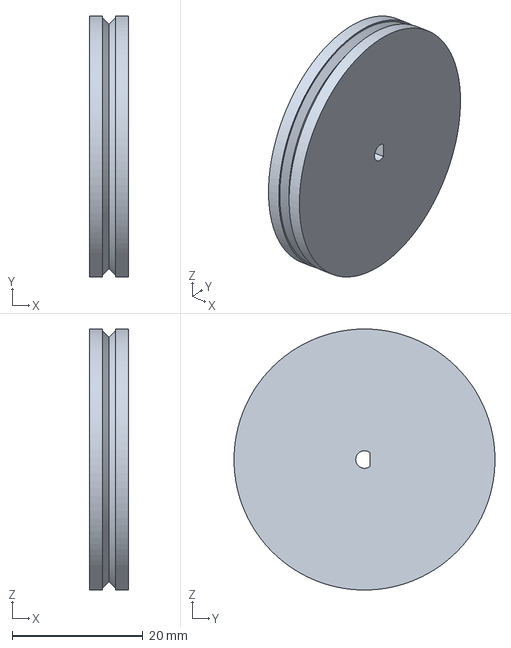
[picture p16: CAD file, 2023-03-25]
Getting Started/Sample CAD Files/Basic Bot Build/Wheel.3mf
6.00 x 40.0 x 40.0 mm

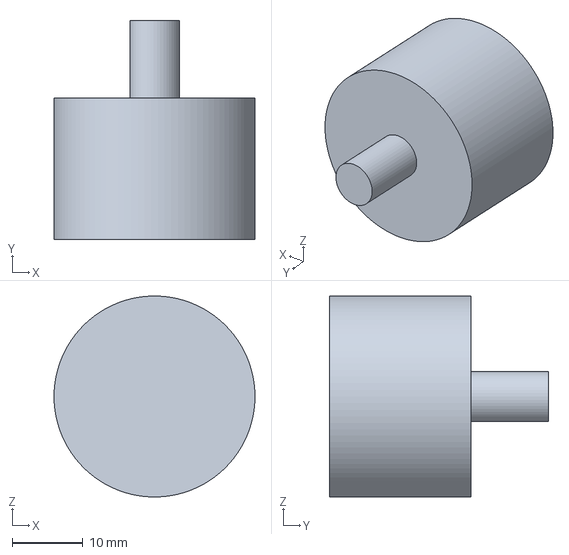
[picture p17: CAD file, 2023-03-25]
Getting Started/Sample CAD Files/Basic Bot Build/BLDC.3mf
28.4 x 31.0 x 28.4 mm

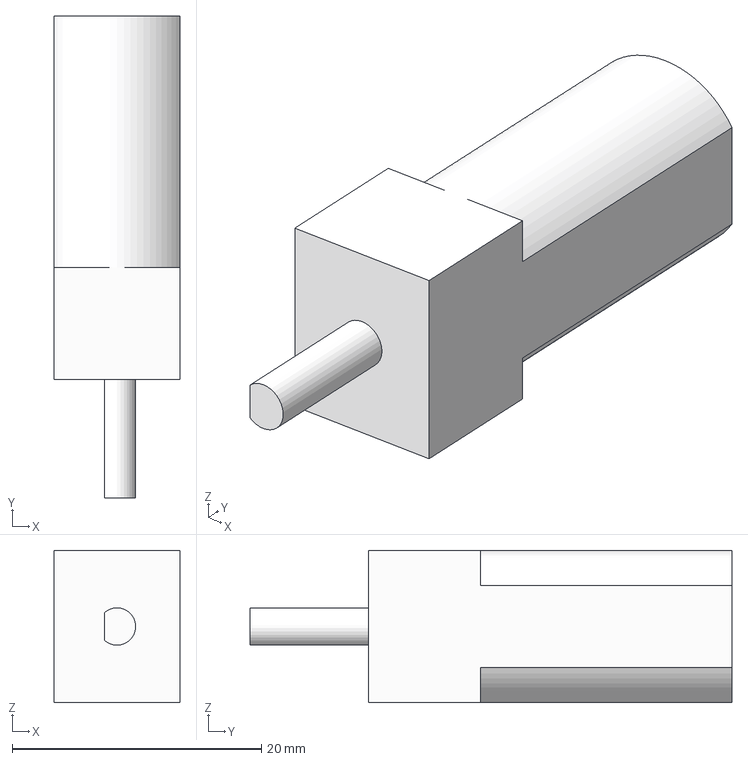
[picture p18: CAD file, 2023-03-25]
Getting Started/Sample CAD Files/Basic Bot Build/DC Motor v1.3mf
10.1 x 38.7 x 12.2 mm

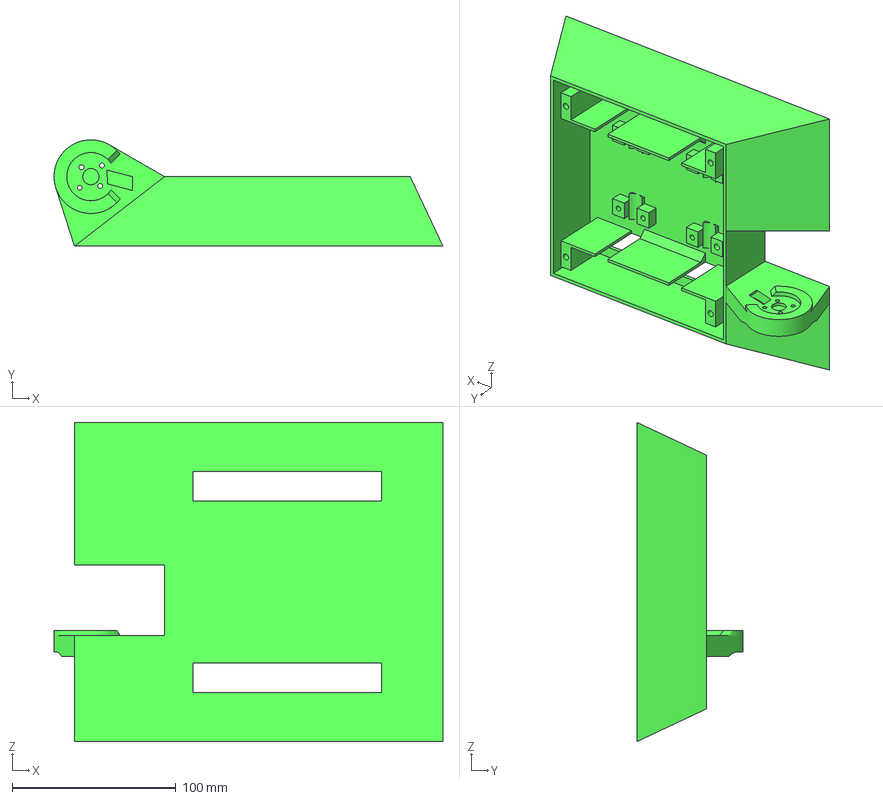
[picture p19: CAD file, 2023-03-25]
Getting Started/Sample CAD Files/Basic Bot Build/Basic Bot Build Body.3mf
237.5 x 65.0 x 195.0 mm

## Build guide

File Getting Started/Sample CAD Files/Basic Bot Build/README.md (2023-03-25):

# Basic Bot Build

Note: This bot is published as it is no longer under active development and is not being maintained by a member of the Watson Combat Robotics League Executive Board. The bot and all files are provided "as-is" and will not be updated in the future.

The components may or may not be accurate, and the bot itself may not be competition worthy. We provided these files in a .3mf format so they can be opened up in your CAD software or 3D printer slicer of choice and can serve as a reference or inspiration in your designs/builds.

Happy building!

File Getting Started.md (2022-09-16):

# Getting Started
## Overview

This document will give you everything you need to know about designing your own combat robot for the Watson Combat Robotics League!

## Conceptual Design

The best way to get ideas for your design if you are new to the concept of combat robotics is to draw inspiration from bots that already exist. Some important things to look for when watching videos are:

- The type of bot (Spinner, flipper, etc)
- Number of competition attachments
- Number of wheels
- Unique design features
- Performance

Once you have some general ideas, sketch them out on a piece of paper, design software, or even on the back of a napkin! Some key things to remember when brainstorming a design of your own:
The type of bot (Spinner, flipper, etc)
Number of competition attachments
Number of wheels
Where will the electronics go?
Where will screws go?

Here are some links to get you started:
- [WCRL YouTube Channel](https://www.youtube.com/channel/UCIaK69JDDWl9wAELpbH6m2w)
- [Team Panic](https://www.youtube.com/c/TeamPanicRobotics)
- [Adelaide Robot Combat](https://www.youtube.com/user/FrydDog)
- [Raptor Robots](https://www.youtube.com/channel/UCBQbgLWFmt3UULC7kQ891VA)
- [3D Power Prints](https://www.youtube.com/channel/UCgO0GEN4iXCauXte8O-5n2w)
- [Maker's Muse](https://youtu.be/YWOqAwXmvJU)

## CAD Design and Part Ordering

Now that you have a conceptual design, you are ready to start designing your bot in CAD (Computer Aided Design)! Just kidding, you’re not quite there yet. You first need to know what is going inside your bot!

### Electronics
#### Microcontroller (Brain of the Bot)

The microcontroller is responsible for sending commands to other components of your robot, (i.e. telling the wheels to spin). Some possible options include:
Arduino

- Nano – Recommended for this project due to the small size
- Uno – Useful for debugging due to built-in header pins, but not necessary
- Mega – Overkill for this project
- Teensy 3.4/4.0/4.1
- Raspberry Pi

#### Bluetooth Transceiver (Communicate with the Bot)

There are many different models of transceiver for this project, however we recommend the [HM-10](https://www.amazon.com/dp/B06WGZB2N4/?coliid=I2803XF5QJ56I&colid=2HZ7F15TNBDGH&psc=1&ref_=lv_ov_lig_dp_it) for this competition as you can use your phone to control the bot via bluetooth. We also recommend using the [Dabble](https://www.arduino.cc/reference/en/libraries/dabble/) phone application for ease of control.

You can use a variety of different transceivers for either remote or bluetooth control, but make sure you select one with good documentation. Our executive team solely uses HM-10’s, so if you think you may need assistance, we recommend selecting that one as well.

#### Controllers (Control the Bot)

Controllers can be as simple as configuring the Dabble app to control motors via your smartphone, or as complicated as designing your own PCB – it is completely up to you and your team!

##### Physical controller requirements/suggestions

- Microcontroller
- Bluetooth module
- Joysticks
- Buttons
- Potentiometers (Useful for controlling CA speed)
- Battery

#### Motors (Move the Bot)

- DC Motors (Recommended for powering wheels)
  - Can be used for powering competition attachments
  - Requires a motor driver board to connect the motors to the microcontroller.
  - When picking your motors be sure to do some calculations to make sure you will have enough voltage and current from the WCRL provided battery.
- Brushless Motors
  - Recommended for Competition Attachments
  - Different from DC motors as they operate with magnetic coils on the inside which turn off and on quickly to spin the motor much faster than a common DC motor can.
  - Requires an Electronic Speed Controller (ESC) rather than a motor driver
- Servos
  - Motor-like device that will act to rotate an arm to a certain position (angle).
  - Many do not allow continuous rotation

These are only some examples – do some research and find all the cool motors you can use!

#### Battery (Power the Bot)

It is recommended that each team use the [WCRL provided battery](https://www.amazon.com/Zeee-Graphene-Quadcopter-Helicopter-Airplane/dp/B07Y67CHJT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)
A team may use their own battery if:

- The Battery is a LiPo (Lithium Polymer)
- The Battery does not exceed 14.8 V (4s) nominally
- The Battery comes with a proper battery bag
- The Battery comes with a charger
- A power switch must cut off power directly from the battery

## Hardware

There are also many miscellaneous parts that are required to build a robot, such as heat-shrink and screws. Please refer to the Build-the-bot BOM for more information.

## CAD Designs
### CAD Software

Now that you know what is going in the bot, you can officially start designing it in CAD. This guide is not going to dive into the intricacies of different CAD softwares or the merits of one CAD software over another. That being said, there are several CAD softwares that you can use:

- Fusion 360 – Recommended by WCRL due to ease of use and student plan
- Creo
- SolidWorks
- SolidEdge
- TinkerCAD

We will be using Fusion360 as a basis for our recommendations. Some useful Fusion360 Resources:
- [Fusion 360 download link](https://www.autodesk.com/campaigns/education/student-design)
- [Fusion 360 tutorials](https://www.youtube.com/watch?v=WKb3mRkgTwg&list=PLrZ2zKOtC_-DR2ZkMaK3YthYLErPxCnT-)
  - We recommend following tutorials prior to attempting to design your bot. This will allow you to familiarize yourself with the interface, and will make designing your bot considerably easier.

## Design Recommendations
- Use parameters to make changing hole sizes for clearance later on easier
- Walls thickness of 2-5 mm
- Use heat-set inserts whenever a screw is going to be inserted
- If you model threads directly into the print, or screw directly into a hole, the plastic will wear out after multiple uses
These are generally a 1-2mm larger than the screw size, but vary based on manufacturer
- A good size for the provided 3mm heat-set inserts is a 4.4mm diameter hole
- Provide clearance for screw heads in the print
- Button vs socket heads are different sizes, and would need different amounts of clearance
Model all components that will go into your bot and create an assembly, so you will know if any parts won’t align properly or will have difficulty fitting in the robot

## 3D Printing Setting Overview

The 3D printer setting overview is found within a different document, [here](https://docs.google.com/document/d/1x-k-k0dfrq4NDOPhjnmKSc4RKWbllCxLYFbABFv0URE/edit?usp=sharing).

- Bot Body Print Settings
- PLA recommended
- Use a 0.3mm layer height if possible to speed up print times
- Use 10-15% Triangle or Honeycomb infill
- Anything above 20% has insignificant strength gain but adds a lot of weight
- 100% infill isn’t as great as it seems
- Print using 4 vertical shells
- Bot Competition Attachment Print Settings
- PETG recommended
- Use a 0.3mm layer height if possible to speed up print times
- Use 25-30% Triangle or Honeycomb infill
- Allow for testing to determine optimum weight balance.
- Heavier CA may actually be a good thing
- Print using 4+ vertical shells

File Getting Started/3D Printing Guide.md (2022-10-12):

# Overview
This document is to serve as a guide for designing parts for FDM 3D printing. This guide is by no means exhaustive, as there are many factors that go into successfully designed and printed parts. We will merely cover the most important aspects from a designing, slicing, and printing perspective.

---

# What is FDM 3D Printing?
Fused Deposition Modeling (FDM) – also called Fused Filament Fabrication (FFF) – 3D printing works by layering melted thermoplastic on top of previous layers to create a three dimensional object.

Common thermoplastics used for 3D printing can be found in the Filament Selection section below.

---

# Workflow
The general workflow for any 3D printed part is as follows:

1. Obtain dimensions
    1. If your part must interface with existing parts, take measurements of those parts using calipers. Keep in mind which dimensions are critical, meaning that they are required to have a good fit.
    2. If your part doesn’t interface with existing parts, have an idea of how large you want your parts to be. This may also be limited by 3D printer size, as we will discuss later in the document.
2. Design in CAD
3. Export .stl or .obj file into a Slicer
4. Slice the file using PrusaSlicer, Cura, Simplify3D, or another slicer software
5. Export G-Code to the printer

---

# CAD Design and Restrictions
This guide is not going to dive into the intricacies of different CAD softwares or the merits of one CAD software over another. That being said, there are several CAD softwares that you can use:

* Fusion 360 – Recommended by WCRL due to ease of use and student plan
* Creo
* SolidWorks
* SolidEdge
* Inventor
* TinkerCAD
* Onshape – Recommended if using a lower performance computer

We will not be covering how to design parts in CAD as there are plenty of resources available. We will instead be focusing on certain part features you will have to keep in mind while designing a part.

Some useful Fusion360 Resources:

* [Fusion 360 download link](https://www.autodesk.com/campaigns/education/student-design)
* [Fusion 360 tutorials](https://www.youtube.com/watch?v=WKb3mRkgTwg&list=PLrZ2zKOtC_-DR2ZkMaK3YthYLErPxCnT-)

We recommend following tutorials prior to attempting to design a part. This will allow you to familiarize yourself with the interface, and will make designing your part considerably easier.

## Printspace

Every 3D printer has a limitation of the size of the objects it can print. The range of each of the three axes determine what is known as the prinspace, or print volume. This means that any single body must fit in that printspace in order to be printed on that machine. Examples of common 3D printers and their printspaces include:

* Prusa i3 MK3S: (25x21x21) cm or (9.84x8.3x8.3) in
* Prusa Mini: (18x18x18) cm or (7x7x7) in

## Overhangs

## Bridging

## Exporting a Mesh

To export a Mesh from Fusion360, open the file for the bodies you want to export. On the left hand navigation panel, select the body you want to export, right click, and select “Save as Mesh”.

From the Save as Mesh navigation menu, select .3MF, .obj, or .stl (binary). Units should always be millimeters. From there, leave refinement as high and click export.

.stl are most commonly used, however, .3MF, .obj, or .stl (binary) can all be imported into a slicer.

[For more information on exporting meshes from Fusion 360, check out the Autodesk Info Page.](https://knowledge.autodesk.com/support/fusion-360/learn-explore/caas/sfdcarticles/sfdcarticles/How-to-export-an-STL-file-from-Fusion-360.html)

---

# Slicing Settings
## What is a slicer?
A slicer takes a mesh file and cuts it horizontally into many layers. The information on how to create each of these layers, including what the nozzle temperature and bed temperature need to be, is then saved into a G-Code file that can be sent to the printer.

## PrusaSlicer
PrusaSlicer is our recommended slicer, as it is designed to work exceptionally well with Prusa brand printers, specifically the Mk3S+ and Mini+. On campus, the Watson Fabrication Lab and the Emerging Technology Studio both have MK3S+ Printers.

PrusaSlicer is free to download, and we would recommend downloading and messing around with it. When you set up the printer profile via the installation wizard, select the MK3S+ with a 0.4mm nozzle.

[Download PrusaSlicer here!](https://www.prusa3d.com/page/prusaslicer_424/)

## Recommended Defaults in PrusaSlicer
## Layer Height
Layer height is the thickness of plastic deposited in each layer. These generally range between 0.15mm - 0.3mm but can go either smaller or larger. The smaller the layer height, the higher the quality in small details, but the longer the print will take.

For most standard prints with details, a 0.2mm layer height will work well. However, for larger or less detailed prints, a 0.3mm layer height will result in a similar quality print that is printed faster.

In the slicer, you can preview different layer heights to visualize how the different layer heights may impact quality on detailed parts.

## Infill
Infill refers both to the percentage of solid material inside of your 3D print as well as the geometric pattern that is present. Your slicer may offer many different pattern options so feel free to do your own experimentation, but generally speaking the strongest geometries are triangular, cubic or gyroidal.

By default most slicers will recommend an infill ranging between 10-20%. This is an ideal infill range as you are optimizing between strength and material usage. However, during early prototyping we would recommend using a very low infill, maybe between 5-10%, in order to provide quicker printing times and save on materials. For prints that your team plans to use for the competition we would recommend using anything between 10-30% infill depending on the application of the printed part. Contrary to what you may think, a higher infill percentage does not always correlate to a stronger part. Using any infill above 45% is almost always a big waste of material and time as the strength is usually maximized at a much lower percentage. The executive team has found that using 20-30% infill and editing the perimeter/walls setting to be 3 or 4 provides great results!

## Print Orientation
Print  orientation is the way in which the part will be printed. As previously mentioned, FDM printers work by printing one layer at a time and building from the bottom to top. Because of this it is important to orient your print in a way such that the bottom of the print is a large flat surface such that it can form a strong connection to the printer’s bed. Additionally you want to make sure that your print is oriented in a way that minimizes the amount of overhangs and bridges and also uses the minimal amount of support materials if any.

## Supports
Supports are 3D printed structures that a slicer will generate over any large bridges or overhangs. Supports can be useful for creating prints that have unique aesthetics but they can be avoided if your design is done well. Often it is best to design your parts to be printed without support materials because it is faster, you do not have to spend time removing the support materials after a print, and supports actually can create a weakened area on your 3D printed part. This is because the support material tends to have a very small gap of air between its last layer and the first layer of your printed part. This small gap allows for slight drooping in the layers directly above the support which provides a weakened section of the print.

In order to avoid needing support materials the executive team recommends the following:

* Any angled sections of your print should be between 90 and 45 degrees with reference to the print bed
* Avoid long bridge like sections, any bridging should be limited to 3 cm or less

## Raft/Skirt/Brim
Rafts, skirts and brims are some additional settings that slicers have to add additional material to the first few layers on the print bed. A raft is a flat surface that is generated between the print bed and your part. Rafts are usually a few layers thick and serve as a good way to stabilize your part if it has a small surface area. Additionally, rafts are great for preventing warping and ensuring good bed adhesion.

Skirts are a small loop that is printed around the perimeter of your part. The executive team always recommends using at least a skirt since it allows for the extruder to be primed and ensure that there is a good flow of filament out of the printer’s nozzle.

A brim is a special type of skirt that is actually connected to the edges of your part. Just like with a raft, a brim is a useful tool to help with bed adhesion. Brims are particularly useful for preventing any slight warping in the edges of parts that already have a large surface area.  

---

# Filament Selection
## PLA
PLA is the most commonly used 3D printing filament. It has outstanding aesthetic characteristics. Bridging and overhangs are much more forgiving with PLA than with any other filament type. Due to its popularity, there are many different variations available that are each optimized for different characteristics. However, in general, parts printed in PLA variants are very rigid, this comes at the expense of a low impact resistance, meaning PLA parts are more likely to shatter than parts printed in other filament types. In addition, parts printed in PLA have relatively poor layer adhesion.

## PETG
PETG is the second most common type of 3D printing filament, it is less rigid than PLA, but its impact resistance is significantly greater than that of any PLA variant.

## TPU
TPU is another common type of 3D printing filament. TPU is much more rubbery than other 3D printing materials. It is best suited for applications that require very high impact resistance and or flexibility.

## ABS
ABS is one of the most commonly used plastics for injection molding. It is more rigid than PETG, but slightly less rigid than PLA. It can be difficult to print, but when done correctly it’s impact resistance is also quite high.

(Note: ETS is not typically printing with ABS currently. Email ETS with any questions)

---

## Pricing
Cost of printing at Binghamton University ETS (Emerging Technology Center) is determined by the amount of material used. This includes support material in addition to your object if needed. For PLA and PETG the price of printing is 0.025 BUC$ (Note: BUC$ are different from meal plans). For reference the following 3d objects and prices are shown:

##### DemoBot:
DemoBotJR

Material Used: 191 grams
Cost at ETS (PLA or PETG): 4.75 BUC$

##### Stump: 
Stump(89 17g)

Material Used: 89.17 grams
Cost at ETS (PLA or PETG): 2.23 BUC$

##### Vase:
Vase(88 24g)

Material Used: 88.24 grans
Cost at ETS (PLA or PETG): 2.21 BUC$

---

# Binghamton University Emerging Technology Studio

The [Binghamton University Emerging Technology Studio](https://www.binghamton.edu/its/about/organization/technology-support-services/innovation/ets/index.html) (ETS) is a makerspace available to all students. They are an excellent 3D printing resource for any questions for Binghamton University Students. 

General hours are:
- Mon-Thurs 10:00-6:00
- Fri 10:00-5:00
- Closed Weekends

Contact ETS for 3D printing help at ETSBing@binghamton.edu

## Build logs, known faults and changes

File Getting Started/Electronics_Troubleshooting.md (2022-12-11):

# Electronics Troubleshooting
---

## Arduino Nano

### Issues Uploading Code

For instances of being unable to upload code to you arduino nano, here are some things to check:

1. Is your Arduino Plugged in (always gotta double check)
2. Ensure HM10 Bluetooth device is disconnected
3. Check that the proper COM port is selected under tools(Tools->Ports). This will depend on your computer
4. Check that you are selecting the proper Arduino that you are using for the project. This can be done by going to Tools->Board: In most cases, this will be an Arduino nano
5. Check which bootloader you have selected; many of the cheaper Arduinos (especially Arduino Nanos) on the market use the “Old Bootloader.” This can be accessed in Tools->Processor
6. You have the correct version of the Arduino IDE

### Windows Does not Recognize Arduino Nano

This may likely be due to the purchase of an off brand Arduino. The most common fix is to check if your Arduino uses a CH430 programming chip on the bottom of your board as the interface between the computer and the programmer. This can be simply fixed by installing the proper drivers from this website. 

http://www.wch-ic.com/downloads/CH341SER_ZIP.html

---

## HM10 Bluetooth Device

### Renaming Device

A WCRL custom PCB is in developement for easy renaming of the HM10 unit.

---

## Sparkfun TB6612 Motor Driver 

### Have the proper drivers

If you are using Sparkfun TB6612 then you will need to install the drivers for the motor driver. These drivers will simplify the implementation of the motor drivers significantly. To install the drivers visit the github website and click the green code button and download Zip.

https://github.com/sparkfun/SparkFun_TB6612FNG_Arduino_Library

Open the Arduino IDE and navigate to the library manager: Sketch->Include library->Add .Zip Library. Find the file you downloaded, select it and click open. The library is now installed.

For more information about the TB6612 drivers, check out sparkfun’s website.

https://learn.sparkfun.com/tutorials/tb6612fng-hookup-guide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

---

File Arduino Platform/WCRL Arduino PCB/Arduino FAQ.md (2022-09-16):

# Arduino FAQ
## My Arduino Nano won’t program?

- This problem typically occurs when incorrect settings are selected in the arduino programmer. Here are some quick checks you can follow to debug.
   - Is your arduino plugged in (always gotta double check that one)
   - Check that the proper COM port is selected under tools(Tools->Ports). This will depend on your computer
   - Check that you are selecting the proper Arduino that you are using for the project. This can be done by going to Tools->Board: In most cases, this will be an Arduino nano
   - Check which bootloader you have selected; many of the cheaper Arduinos (especially Arduino Nanos) on the market use the “Old Bootloader.” This can be accessed in Tools->Processor

## My Arduino Nano is not recognized on Windows?
- This is most likely due to the purchase of an off brand Arduino. The most common fix is to check if your Arduino uses a CH430 programming chip on the bottom of your board as the interface between the computer and the programmer. This can be simply fixed by installing the proper drivers from this website.
  - To install extract the .zip file and double click the SETUP application, click yes on the pop-up, and click install

## Installing Sparkfun TB6612 Drivers
- If you are using Sparkfun TB6612 then you will need to install the drivers for the motor driver. These drivers will simplify the implementation of the motor drivers significantly. To install the drivers visit the github website and click the green code button and download Zip.
- Open the Arduino IDE and navigate to the library manager: Sketch->Include library->Add .Zip Library. Find the file you downloaded, select it and click open. The library is now installed.
- For more information about the TB6612 drivers, check out sparkfun’s website.

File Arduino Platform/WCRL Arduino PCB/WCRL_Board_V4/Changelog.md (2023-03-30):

# Changes from V3

- Rerouted all traces, increased tracewidth for several traces
- Solid ground plane
- Flipped the motor driver (Please note that the VM is in the correct location when installing the motor driver. Motor drivers from V3 may not be a drop-in replacement due to incorrectly installed header pins)
- Rotated the motor driver counter-clockwise 90 degrees
- Shortened the board by 2-3 mm

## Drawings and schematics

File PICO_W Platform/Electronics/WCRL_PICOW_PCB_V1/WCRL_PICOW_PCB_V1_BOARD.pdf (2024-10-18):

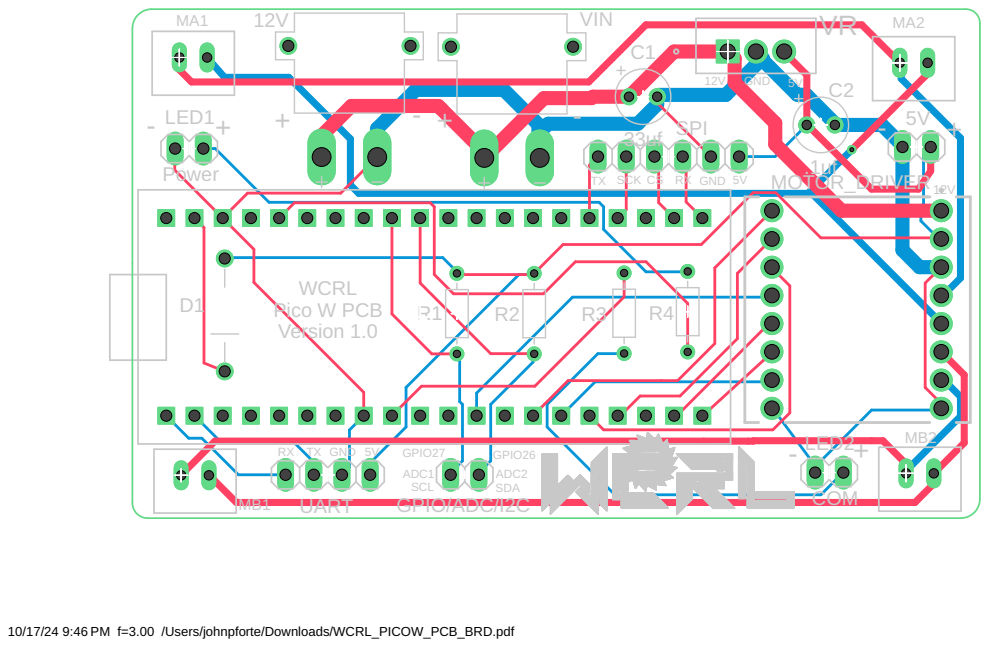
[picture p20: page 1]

TX SCK CS RX GND 5V

10/17/24 9:46 PM f=3.00 /Users/johnpforte/Downloads/WCRL_PICOW_PCB_BRD.pdf

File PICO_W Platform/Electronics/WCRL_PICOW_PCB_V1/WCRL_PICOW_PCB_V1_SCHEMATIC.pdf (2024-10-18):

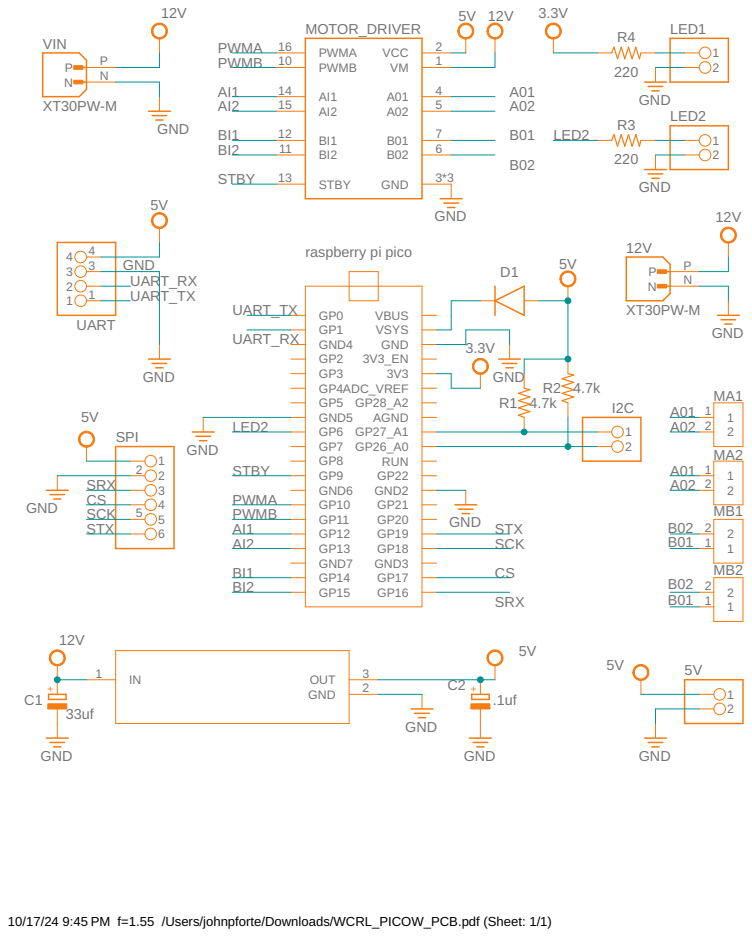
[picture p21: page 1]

10/17/24 9:45 PM f=1.55 /Users/johnpforte/Downloads/WCRL_PICOW_PCB.pdf (Sheet: 1/1)

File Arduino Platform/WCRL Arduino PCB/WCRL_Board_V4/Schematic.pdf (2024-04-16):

TB6612

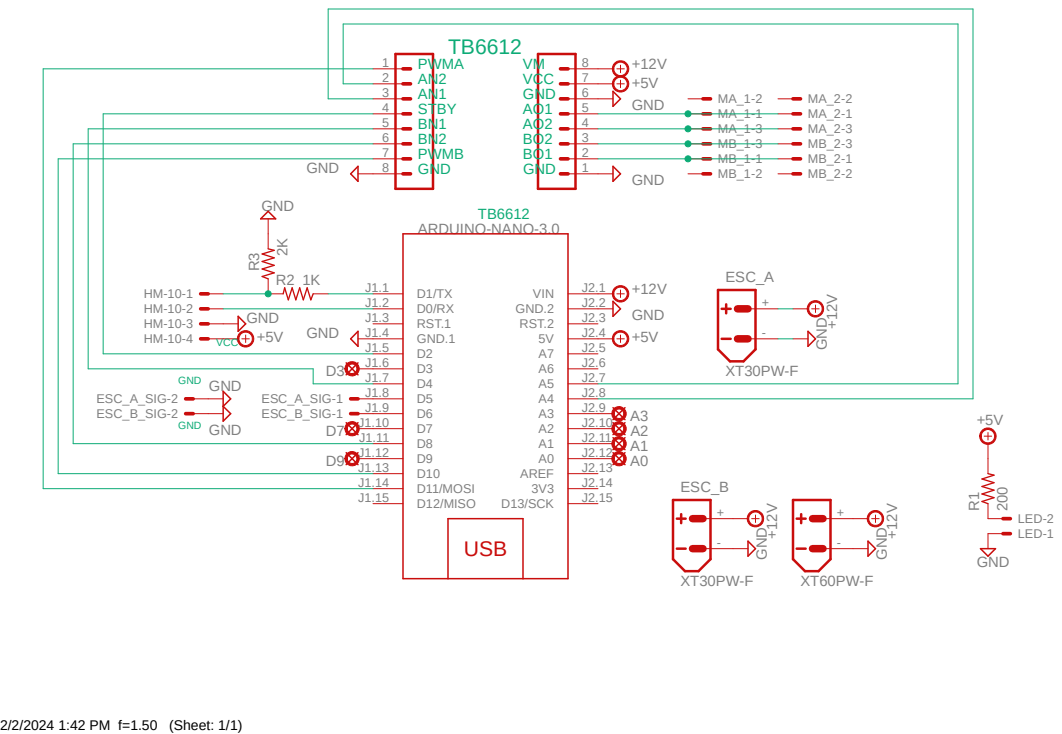
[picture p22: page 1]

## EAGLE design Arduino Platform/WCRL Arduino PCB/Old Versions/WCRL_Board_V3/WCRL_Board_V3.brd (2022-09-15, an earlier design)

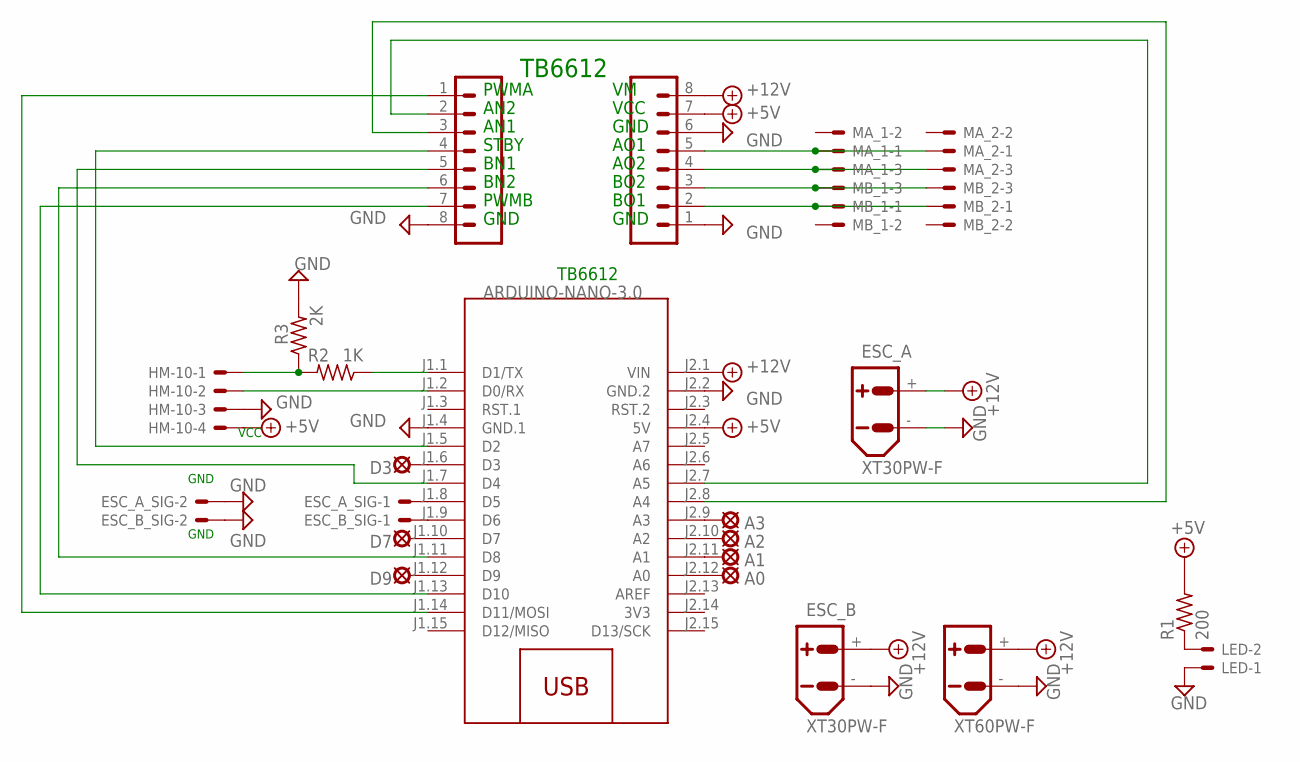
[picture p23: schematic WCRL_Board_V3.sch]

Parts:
A0, A1, A2, A3: LSP10
BATTERY: XT60PW-F
D3, D7, D9: LSP10
ESC_A: XT30PW-F
ESC_A_SIG: JST-XH-02-PIN-LONG-PAD; JST-XH-02-PACKAGE-LONG-PAD
ESC_B: XT30PW-F
ESC_B_SIG: JST-XH-02-PIN-LONG-PAD; JST-XH-02-PACKAGE-LONG-PAD
HM-10: JST-XH-04-PIN-LONG-PAD; JST-XH-04-PACKAGE-LONG-PAD
J1, J2: CONN_08NO_SILK_FEMALE_PTH; 1X08_NO_SILK
LED: JST-XH-02-PIN-LONG-PAD; JST-XH-02-PACKAGE-LONG-PAD
M1: ARDUINO-NANO-3.0
MA_1, MA_2: JST-XH-03-PIN-LONG-PAD; JST-XH-03-PACKAGE-LONG-PAD
MB_1, MB_2: JST-XH-03-PIN-LONG-PAD; JST-XH-03-PACKAGE-LONG-PAD
R1: 200; 0204/5
R2: 1K; 0204/5
R3: 2K; 0204/5

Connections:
3V3: M1.J2.14 (3V3)
+5V: HM-10.4, J1.7, M1.J2.4 (5V), R1.2
+12V: BATTERY.+, ESC_A.+, ESC_B.+, J1.8, M1.J2.1 (VIN)
GND: BATTERY.-, ESC_A.-, ESC_A_SIG.2, ESC_B.-, ESC_B_SIG.2, HM-10.3, J1.1, J1.6, J2.8, LED.1, M1.J1.4 (GND.1), M1.J2.2 (GND.2), R3.2
unnamed: D3.MP, M1.J1.6 (D3)
unnamed: D7.MP, M1.J1.10 (D7)
unnamed: D9.MP, M1.J1.12 (D9)
unnamed: HM-10.1, R2.2, R3.1
unnamed: ESC_A_SIG.1, M1.J1.8 (D5)
unnamed: ESC_B_SIG.1, M1.J1.9 (D6)
unnamed: M1.J1.1 (D1/TX), R2.1
unnamed: J2.4, M1.J1.5 (D2)
unnamed: J2.3, M1.J2.8 (A4)
unnamed: J1.5, MA_1.1, MA_2.1
unnamed: J1.4, MA_1.3, MA_2.3
unnamed: J1.2, MB_1.1, MB_2.1
unnamed: J1.3, MB_1.3, MB_2.3
unnamed: HM-10.2, M1.J1.2 (D0/RX)
unnamed: J2.2, M1.J2.7 (A5)
unnamed: J2.5, M1.J1.7 (D4)
unnamed: J2.6, M1.J1.11 (D8)
unnamed: LED.2, R1.1
unnamed: J2.7, M1.J1.13 (D10)
unnamed: J2.1, M1.J1.14 (D11/MOSI)
unnamed: A3.MP, M1.J2.9 (A3)
unnamed: A1.MP, M1.J2.11 (A1)
unnamed: A0.MP, M1.J2.12 (A0)
unnamed: A2.MP, M1.J2.10 (A2)

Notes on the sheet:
PWMA
GND
VCC
AO1
AO2
BO2
BO1
AN2
AN1
STBY
BN1
BN2
PWMB
TB6612

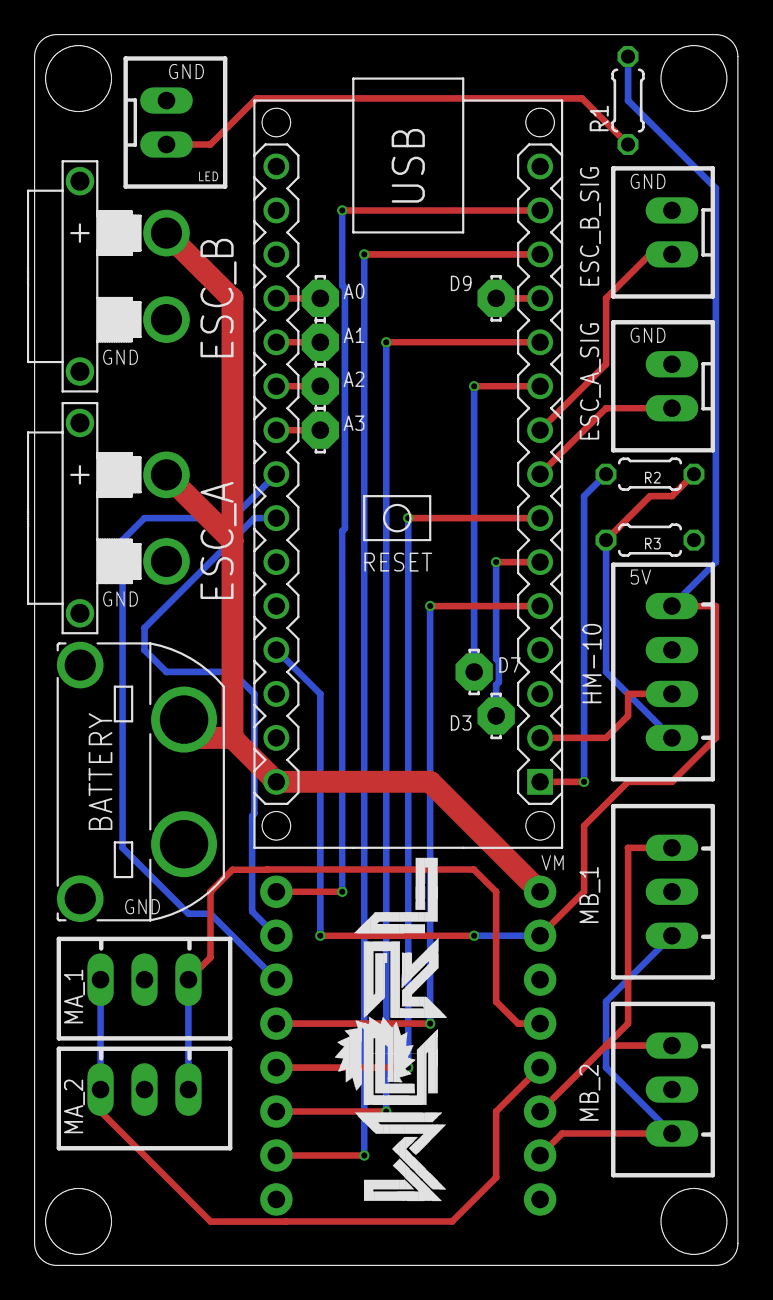
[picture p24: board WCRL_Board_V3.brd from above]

Board: 2 copper layers, 40.6 x 71.1 mm, 24 parts (1 on the bottom side), 27 nets.

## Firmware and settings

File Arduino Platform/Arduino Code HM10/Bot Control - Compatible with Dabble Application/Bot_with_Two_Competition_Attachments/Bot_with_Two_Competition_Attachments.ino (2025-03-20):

/*
    This example code was authored and/or compiled by the Watson Combat Robotics League for use on the Build-The-Bot Platform.
    This code is open source as per the MIT license found on the WCRL Github Page (https://github.com/wcrl/Build-the-Bot/blob/eadc81d94e1f041c1e13751ea7d3190f495dc393/LICENSE)
    Last Revised: 2022-10-18
*/

#include <Dabble.h>
/*
   This code utilizes the Dabble Library for bluetooth control of the robot.
   However, a modification must be made to the library to allow for hardware serial instead of software serial.
   1. Download the Dabble library via the Arduino IDE
   1. Open the Dabble.cpp file and change "Serial<#>.begin" to "Serial.begin"
   2. In the same .cpp file change "DabbleSerial=&Serial<#>" to "DabbleSerial=&Serial"
   3. NOTE: While Dabble bluetooth connection is active code may not be uploaded to the arduino
*/

#include <Servo.h>   //Runs the PWM for the ESC
Servo ESC1;          // Create servo object to control the ESC1
Servo ESC2;          // Create servo object to control the ESC2

#include <SparkFun_TB6612.h> // Motor Driver Library provided by Sparkfun

//Left Wheel is Motor A on the PCB
#define L_Wheel_in1 A5  //A4
#define L_Wheel_in2 A4  //A5
#define L_Wheel_PWM 11  //D11

//Left Wheel is Motor B on the PCB
#define R_Wheel_in1 4   //D4
#define R_Wheel_in2 8   //D8
#define R_Wheel_PWM 10  //D10

const int motor_offset = -1;
#define STBY 2
Motor L_Wheel(L_Wheel_in1, L_Wheel_in2, L_Wheel_PWM, motor_offset, STBY);
Motor R_Wheel(R_Wheel_in1, R_Wheel_in2, R_Wheel_PWM, motor_offset, STBY);

#define CUSTOM_SETTINGS
#define INCLUDE_GAMEPAD_MODULE


void setup() {

  Serial.begin(250000);       // make sure your Serial Monitor is also set at this baud rate.
  Dabble.begin(9600, 0, 1);   //(Baudrate, rx,tx) Enter baudrate of your bluetooth. Connect bluetooth on Bluetooth port present on evive (in Dabble Library Example).
  ESC1.attach(5, 1000, 2000);  // D5 
  ESC1.write(0);               // Sets the speed to 0
  ESC2.attach(6,1000,2000);     // D6
  ESC2.write(0);               // Sets speed to 0
}

void loop() {
  Dabble.processInput();      //this function is used to refresh data obtained from smartphone. Hence calling this function is mandatory in order to get data properly from your mobile.

  //Motion Control
  if (GamePad.isUpPressed())  //Move forward
  {
    L_Wheel.drive(255);
    R_Wheel.drive(-255);
  }
  else if (GamePad.isDownPressed()) //Move backward
  {
    L_Wheel.drive(-255);
    R_Wheel.drive(255);
  }
  else if (GamePad.isLeftPressed()) { //Move left
    L_Wheel.drive(-255);
    R_Wheel.drive(-255);
  }
  else if (GamePad.isRightPressed()) { //Move right
    L_Wheel.drive(255);
    R_Wheel.drive(255);
  }
  else {  //Idle
    L_Wheel.drive(0);
    R_Wheel.drive(0);
  }

  //Competition Attachment (Weapon) Control
  
  if (GamePad.isTrianglePressed())  //Start up Competition attachments. Low speed mode
  {
    ESC1.write(45);
    ESC2.write(45);
    Serial.print("Triangle");
  }
  if (GamePad.isCirclePressed())  //Increases the speed of the competition attachments. High speed mode
  {
    ESC1.write(70);
    ESC2.write(70);
    Serial.print("Circle");
  }
  if (GamePad.isCrossPressed()) //Shuts off the competition attachments
  {
    ESC1.write(0);
    ESC2.write(0);
    Serial.print("Cross");
  }

  if (GamePad.isStartPressed()) //Idle
  {

    Serial.print("Start");
    delay(100);
  }

  delay(100);

}

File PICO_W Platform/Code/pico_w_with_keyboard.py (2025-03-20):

import network
import socket
from machine import Pin, PWM
import time

led = Pin(6, Pin.OUT)
 
# Set up ESC control on GPIO27 (PWM)
esc = PWM(Pin(1), freq=50)
  # Most ESCs operate at 50Hz

stby = Pin(9, Pin.OUT)
stby.value(1)

# Define motor control pins for the TB6612 module (same as before)
AIN1 = Pin(12, Pin.OUT)
AIN2 = Pin(13, Pin.OUT)
PWMA = PWM(Pin(10))
PWMA.freq(100)#lower this value if the esc buttons control the drive motor

BIN1 = Pin(14, Pin.OUT)
BIN2 = Pin(15, Pin.OUT)
PWMB = PWM(Pin(11))
PWMB.freq(100)

def arm_esc():
    print("Arming ESC...")
    esc.duty_u16(6554)
    time.sleep(2)
    esc.duty_u16(3277)
    #control_esc('brake')  # Arm with brake (1ms pulse)
    for _ in range(6):  # Blink LED 6 times while arming
        led.toggle()
        time.sleep(0.5)
     # Continue holding brake
    time.sleep(1)  # ESC arm delay

# Function to control the ESC
def control_esc(level):
    if level == 'brake':
        duty = 3277  # Brake, 1ms pulse width
    elif level == 'half':
        duty = 4915  # Half-speed, around 1.5ms pulse width
    elif level == 'full':
        duty = 6554  # Full-speed, around 2ms pulse width
    esc.duty_u16(duty)

# Function to control the motors
def control_motor(motor, direction, speed):
    if motor == '1':
        if direction == 'forward':
            AIN1.on()
            AIN2.off()
        elif direction == 'backward':
            AIN1.off()
            AIN2.on()
        elif direction == 'left':
            AIN1.on()
            AIN2.off()
        elif direction == 'right':
            AIN1.off()
            AIN2.on()
        else:
            AIN1.off()
            AIN2.off()
        PWMA.duty_u16(speed)
    
    elif motor == '2':
        if direction == 'forward':
            BIN1.on()
            BIN2.off()
        elif direction == 'backward':
            BIN1.off()
            BIN2.on()
        elif direction == 'left':
            BIN1.off()
            BIN2.on()
        elif direction == 'right':
            BIN1.on()
            BIN2.off()
        else:
            BIN1.off()
            BIN2.off()
        PWMB.duty_u16(speed)

def web_page():
    html = """<!DOCTYPE html>
    <html>
    <head>
    <title>Pico W Gamepad Control</title>
    <style>
    body {
        font-family: Arial, sans-serif;
        text-align: center;
        margin-top: 50px;
        background-color: #f8f9fa; /* Light background for better contrast */
    }
    .button {
        display: inline-block;
        padding: 20px;
        margin: 10px;
        font-size: 20px;
        color: white;
        background-color: #007bff;
        border: none;
        border-radius: 5px;
        cursor: pointer;
        width: 120px; /* Slightly wider buttons */
    }
    .button:hover {
        background-color: #0056b3;
    }
    .container {
        display: flex;
        justify-content: center;
        align-items: flex-start; /* Align items to the start */
    }
    .gamepad {
        display: grid;
        grid-template-columns: repeat(3, 1fr);
        grid-gap: 10px;
        justify-content: center;
        margin-right: 200px; /* Space between gamepad and esc-control */
        width: 250px;
    }
    .esc-control {
        display: flex;
        flex-direction: column;
        justify-content: center;
        align-items: center;
        height: 300px; /* Set a fixed height if needed */
    }
    </style>
    <script>
    document.addEventListener('keydown', function(event) {
        switch(event.key) {
            case 'w':
                location.href = '/forward';
                break;
            case 'a':
                location.href = '/left';
                break;
            case 's':
                location.href = '/backward';
                break;
            case 'd':
                location.href = '/right';
                break;
            case ' ':
                location.href = '/stop';
                break;
            case 'f':
                location.href = '/esc?mode=full';
                break;
            case 'h':
                location.href = '/esc?mode=half';
                break;
            case 'b':
                location.href = '/esc?mode=brake';
                break;
        }
    });
    </script>
    </head>
    <body>
    <h1>ESC and Motor Control Gamepad</h1>

    <div class="container">
        <div class="gamepad">
            <div></div>
            <div><button class="button" onclick="location.href='/forward'">Forward</button></div>
            <div></div>
            <div><button class="button" onclick="location.href='/left'">Left</button></div>
            <div><button class="button" onclick="location.href='/stop'">Stop</button></div>
            <div><button class="button" onclick="location.href='/right'">Right</button></div>
            <div></div>
            <div><button class="button" onclick="location.href='/backward'">Backward</button></div>
            <div></div>
        </div>
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

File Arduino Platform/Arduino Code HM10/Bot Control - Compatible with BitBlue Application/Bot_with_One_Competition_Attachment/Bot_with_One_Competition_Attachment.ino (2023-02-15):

/* Danny Iacobacci | Watson Combat Robotics League | 2023-02-14
* This code is compatible with the "BitBlue" app
*
* Note: Pressing and holding does NOT function properly. This is a design conflict in the 
* BitBlue application. Instead, pressing the button once will trigger an action. Pressing
* the button again will end that action.
* 
* Controls:
* Forward Arrow: Move Bot Forward
* Back Arrow: Move Bot in Reverse
* Left Arrow: Move Bot to the Left
* Right Arrow: Move Bot to the Right
* A: Competition Attachment at Low Speed (Defined Below)
* X: Competition Attachment at High Speed (Defined Below)
* B: Not Used
* Y: Not Used
* Start: Not Used
* Select: Not Used
*/

//Software Serial for BT Control Setup and Variable Declarations
#include <SoftwareSerial.h>
SoftwareSerial BTserial(0, 1);
char lastInput;

//Servo initialization for BLDC motors
#include <Servo.h>  //Runs the PWM for the ESC
Servo ESC;          // Create servo object to control the ESC

//Change these to modify your BLDC speed
#define BLDC1_Speed_Low 35
#define BLDC1_Speed_High 70

//Drive motor declarations
#include <SparkFun_TB6612.h>  // Motor Driver Library provided by Sparkfun

//Left Wheel is Motor A on the PCB
#define L_Wheel_in1 A5  //A4
#define L_Wheel_in2 A4  //A5
#define L_Wheel_PWM 11  //D11

//Left Wheel is Motor B on the PCB
#define R_Wheel_in1 4   //D4
#define R_Wheel_in2 8   //D8
#define R_Wheel_PWM 10  //D10

const int motor_offset = -1;
#define STBY 2
Motor L_Wheel(L_Wheel_in1, L_Wheel_in2, L_Wheel_PWM, motor_offset, STBY);
Motor R_Wheel(R_Wheel_in1, R_Wheel_in2, R_Wheel_PWM, motor_offset, STBY);

//Toggles for button presses. Turns on with the first press, turns off with the second press
bool forwardCheck = true;
bool reverseCheck = true;
bool rightCheck = true;
bool leftCheck = true;
bool ca1CheckLow = true;
bool ca1CheckHigh = true;

void setup() {
  Serial.begin(9600);
  BTserial.begin(9600);       // make sure your Serial Monitor is also set at this baud rate.  //(Baudrate, rx,tx) Enter baudrate of your bluetooth. Connect bluetooth on Bluetooth port present on evive (in Dabble Library Example).
  ESC.attach(5, 1000, 2000);  // Initializes the ESC  ---- Pin 5 = ESC A; Pin 6 = ESC B
  ESC.write(0);               // Sets the speed to 0
}

void loop() {
  //Motion Control

  //Checks to see if the BT serial is available, and if it is, takes the lastInput from the buffer
  if (BTserial.available()) {
    lastInput = BTserial.read();
    Serial.println(lastInput);
    delay(5);
  }

  if (lastInput == 'F')  //Move forward
  {
    if (forwardCheck) {
      L_Wheel.drive(255);
      R_Wheel.drive(-255);
      forwardCheck = false;  //Switches the toggle
      lastInput = "";        //Resets the last input to not get stuck repeatedly toggling on/off
    } else {
      L_Wheel.drive(0);
      R_Wheel.drive(0);
      forwardCheck = true;
      lastInput = "";
    }
  } else if (lastInput == 'B')  //Move backward
  {
    if (reverseCheck) {
      L_Wheel.drive(-255);
      R_Wheel.drive(255);
      reverseCheck = false;
      lastInput = "";
    } else {
      L_Wheel.drive(0);
      R_Wheel.drive(0);
      reverseCheck = true;
      lastInput = "";
    }
  } else if (lastInput == 'L') {
    if (leftCheck) {
      L_Wheel.drive(-255);
      R_Wheel.drive(-255);
      leftCheck = false;
      lastInput = "";
    } else {
      L_Wheel.drive(0);
      R_Wheel.drive(0);
      leftCheck = true;
      lastInput = "";
    }
  } else if (lastInput == 'R') {
    if (rightCheck) {
      L_Wheel.drive(255);
      R_Wheel.drive(255);
      rightCheck = false;
      lastInput = "";
    } else {
      L_Wheel.drive(0);
      R_Wheel.drive(0);
      rightCheck = true;
      lastInput = "";
    }
  }

  //Competition Attachment(Weapon) Control
  if (lastInput == 'A')  //Competiton Attachment on low speed
  {
    if (ca1CheckLow) {
      ESC.write(BLDC1_Speed_Low);
      ca1CheckLow = false;
      lastInput = "";
    } else {
      ESC.write(0);
      ca1CheckLow = true;
      lastInput = "";
    }
  }
  if (lastInput == 'X')  //Competiton Attachment on High speed
  {
    if (ca1CheckHigh) {
      ESC.write(BLDC1_Speed_High);
      ca1CheckHigh = false;
      lastInput = "";
    } else {
      ESC.write(0);
      ca1CheckHigh = true;
      lastInput = "";
    }
  }
}

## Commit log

2022-09-14 Adding PCB V2
    [WCRL_Board_V2.brd, WCRL_Board_V2.sch]
2022-09-14 Adding in PCB BOM
    [WCRL_Board_V2.xlsx]
2022-09-14 Moving BOM
    [WCRL_Board_V2.xlsx]
2022-09-14 Trying ODS
    [Copy of WCRL_Board_V2.ods]
2022-09-14 Removing failed BOMs
    [Copy of WCRL_Board_V2.ods, WCRL_Board_V2.xlsx]
2022-09-15 Add Board V3
    [WCRL_Board_V2.brd, WCRL_Board_V2.sch, WCRL_Board_V3.brd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]
2022-09-16 Add BOM
2022-09-16 Update BOM
2022-09-20 Addition of Pictures
    Finding it difficult becoming accustomed to Git and GitHub. Spent too long thinking there was a complicated way to insert the photos and learned there was an upload spot. I have no idea how to size them. On the screen shot it says "width" but not in the downloaded image of Groot.
2022-09-23 Update 3D Printing Guide.md
    Swap baby groot for sc of stump print. Addition or PETG option because same price as PLA at ETS
2022-09-23 Update 3D Printing Guide.md
2022-09-23 Updated BOM with new links
2022-10-06 Update Electronics BOM.md
2022-10-19 Update Bot_with_One_Competition_Attachment.ino
    All I did was add a note to the code reminding that Arduino code cannot be uploaded while dabble is active and slightly change the weapon speed values in case Dillon's hunch is right.
2022-11-10 Add PCB v3 Images
2023-01-13 Spring 2023 Rule Revisions
2023-03-25 Add BBB
    [22x2 O Ring.3mf, BLDC.3mf, Ball Bearing.3mf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]
2023-03-30 Added V4
    [WCRL_Board_V4.brd, WCRL_Board_V4.sch]
2023-09-29 Update Electronics BOM.md
    Luke R.
2023-10-06 L298N_Schematic
    Schematic for the L298N motor driver, pictures included for clarification to make it fit with the V3 PCB
    [L298N_Schematic_v1.sch]
2023-10-22 L298 Schematic image
    Little easier to view than opening up Eagle or Fusion
2024-02-06 Add files via upload
    Autonomous Wiring, both pdf and actual schematic file for easier viewing
    [Autonomous_v1.sch]
2024-03-15 arena code for 2 servos and brushless motor (#45)
2024-09-08 Updated and Organized
    Platform Separation alongside main parts library
    [Autonomous_v1.sch, L298N_Schematic_v1.sch, N20 Motor.step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]
2024-09-08 Simplify
    Sample Bod CAD into Getting Started
    [22x2 O Ring.3mf, BLDC.3mf, Ball Bearing.3mf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]
2024-10-18 Electrical
    Added more Pico W files
    Updated Readme

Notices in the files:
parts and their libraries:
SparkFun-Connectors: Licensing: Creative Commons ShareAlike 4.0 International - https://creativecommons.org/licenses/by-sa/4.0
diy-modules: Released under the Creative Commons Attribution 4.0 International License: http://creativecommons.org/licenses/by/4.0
